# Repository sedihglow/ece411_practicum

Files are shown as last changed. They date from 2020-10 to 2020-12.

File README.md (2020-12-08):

# ece411_practicum
ece411 practicum project Team 16

# how to upload to ESP
1. Start upload from arduino IDE.
  - It will sit on connecting for this time.
2. Pull the reset pin low or unplug the device
3. Pull GPIO2 low with a button.
4. Let the reset pin go high or plug back in the device while gpio2 is low
  - The code should start uploading
5. let go of the GPIO2 button to ground.

# ESP setup program
1. Setup sensor pins
2. Setup I2C for moisture sensor
3. Try to connect to wifi using credentials in EEPROM
4. If credentials are bad, start a wifi hotspot on ESP
5. Connect to ESP using its wifi hotspot by connecting to the IP Address from a web browser
6. Once credentials are changed it reconnects using the new credentials.

# ESP main loop program flow
1. Check for user packet
2. if user sent a packet, handle the request for moisture threshold or pump time
3. read the moisture sensor
4. If the moisture sensor reads below threshold and water is in the tank, water plant
5. repeat 1-4

# user program
To compile use the makefile $make
To run you can use the makefile $make run
The user program will prompt the user with a menu
  - change moisture threshold
  - change pump time
  - exit program
  
The moisture threshold can be values of 1 to 1000

The pump time can be between 1 and 10 seconds

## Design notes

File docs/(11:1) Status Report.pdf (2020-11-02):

The Four COVIDeers
11/1/2020
Week 5 Status Report

Now that we are at the end of week five, our pace has started to pick up. Our main goals were to have all components in hand, test the components, and to have some prototypes by this time. We almost have all of the components, which are being tested, and have made some low-level prototypes.

We have completed a preliminary schematic and have begun working on our PCB design using Eagle CAD. Our team has also started to make a voltage regulator circuit for our esp8266 microcontroller. In the next two weeks, we plan on assembling our product and doing a large amount of coding. This would set aside the last few weeks for troubleshooting and making corrections.

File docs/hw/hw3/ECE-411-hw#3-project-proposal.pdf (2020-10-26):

# Project Design Specification

## The “Smart Irrigator”

Authors: Jakob White, Nathan Paul, Ahmad Alothaimin, James Ross

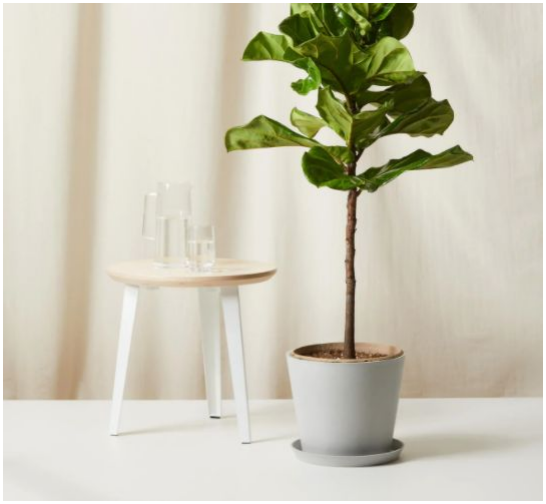
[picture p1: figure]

Date: Oct. 20, 2020
Version: 1.0

Concept of Operations

- Need Statement
Today, work occupies a majority of an individual’s time. Sometimes, a person might not be able to take care of their plants due to distractions. Being out of town for a period of time could also result in a house plant dying from lack of water. An irregular watering schedule for your plants could also lead to problems for the plants. Therefore, it is desirable to have an automated system to care for the plants.
- Objective Statement
What is our solution? The Smart Irrigator system can be a new addition to smart home devices in a society where home automation is taking off. It is an auto-irrigation system intended for small-scale indoor plants that automatically hydrates the soil depending on the current moisture level in the soil. Therefore, rather than worrying about whether or not you watered your plants, the Smart Irrigator will automatically do it for you.
- Who Uses It? Why?
This watering system can be used by horticulturalists, hobbyists, or anyone who owns a small-scale indoor plant. To use this system, the user will first set up their chosen plant with the Smart Irrigator (including a water reservoir of their choice). They will then use our app on their laptop to customize their plant-watering preferences, which will include options for either a timer-based watering schedule or fully-automated, sensor-based watering.

Market Analysis

This product is intended for anyone with an interest in growing small-scale indoor plants, but does not want to spend too much time tending to them. This device will particularly be directed towards people in the age range of 20-35 years old who own house plants. As for competition, there are a few products that are similar to ours. One competitor is the MAYiT Garden Automatic Drip watering system, which uses a timer to water the plants. Many other competitors also have timers, and some must even be plugged into an outlet. Our product will be different because it will use a moisture sensor that will detect when the plant needs to be watered, which will then activate a pump. Our device will be powered by batteries and will also notify the user when more water needs to be added to the reservoir. Given the materials we expect to use, the unique features of our product, and the widespread interest in having indoor plants among various demographics (coupled with a disinterest in maintaining them), we expect to sell our product at around $50.

Requirements

- Functionality
- The product must sense moisture level in the soil of small-scale potted plants.
- The product must receive user input to establish a watering schedule.
- The product must sense the water level in the water reservoir.
- The product must process input from the moisture sensor to determine whether the plant needs to be watered.

- The product must process input from the water-level sensor to determine whether or not the water reservoir is empty.
- When the plant needs water, the product must actuate a water pump to water the plant.
- When the reservoir is empty, the product must not actuate the water pump.
- The product should notify the user if the water reservoir is empty.
- The product may notify the user if batteries are low.
- The product may monitor the plant’s exposure to natural sunlight to provide artificial sunlight if the plant is not properly exposed.
- The product must employ Wi-Fi to enable the user to change his watering preferences.
- The product should operate using an Arduino program.
- Energy
- The product should be battery operated.
- The product should have a battery life of at least one month.
- The product may be solar powered.
- Operational
- The product should be adaptable to any small-scale potted plant.
- Maintainability
- The product should notify the user when an error occurs in the system.

System Architecture

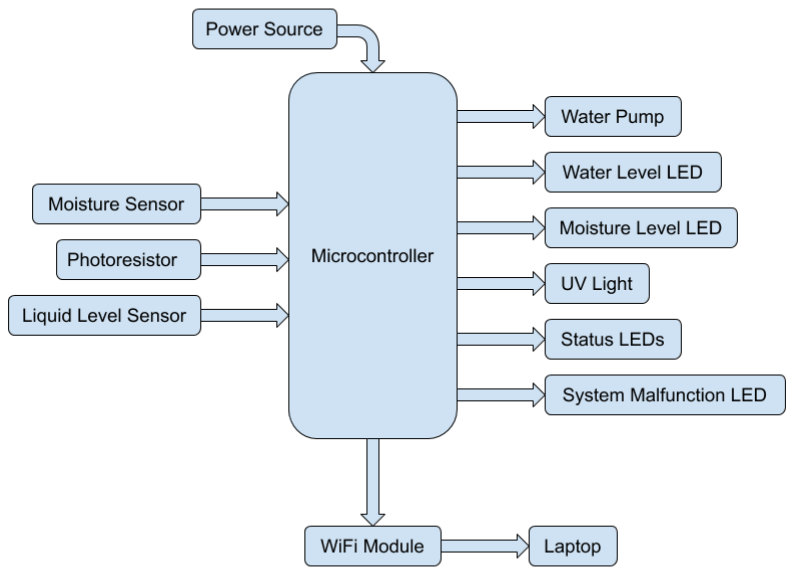
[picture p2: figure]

Figure I: Level I diagram of the Smart Irrigator

Design Specification

- Sensors
- Non-contact Digital Water/Liquid Level Sensor
- Analog Capacitive Soil Moisture Sensor
- Processor
- Esp8266 nodemcu
- Actuator
- Water Pump
- Multicolor LEDs
- Power
- 3.3V voltage regulator
- 3.7V lithium ion polymer battery
- Development Environment
- Arduino IDE

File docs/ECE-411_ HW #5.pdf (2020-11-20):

Names: Jakob White, Nathan Paul, Ahmad Alothaimin, James Ross Date: Nov. 19, 2020

# Detailed Design

Level-0 Design

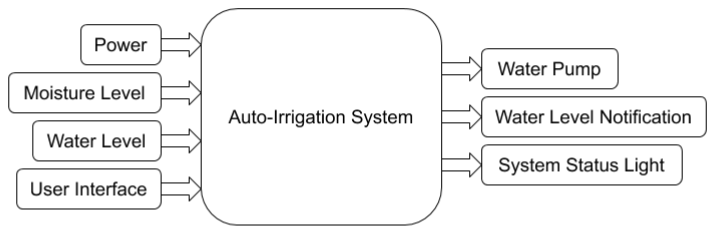
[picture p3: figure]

Module | Auto-Irrigation System
Inputs | Power: 3.6V Moisture Level: Variable Water Level: Variable User Interface: Variable (Watering Schedule Control)
Outputs | Water Pump: Water to Plant Water Level Notification: WiFi Notification to Refill Reservoir System Status Light: Light Indicating System Status
Functionality | This system automatically waters indoor plants. If the moisture level is below a certain level and the water reservoir is not empty, the plant is watered. Else, the plant is not watered. The user should be notified when the water reservoir is empty.

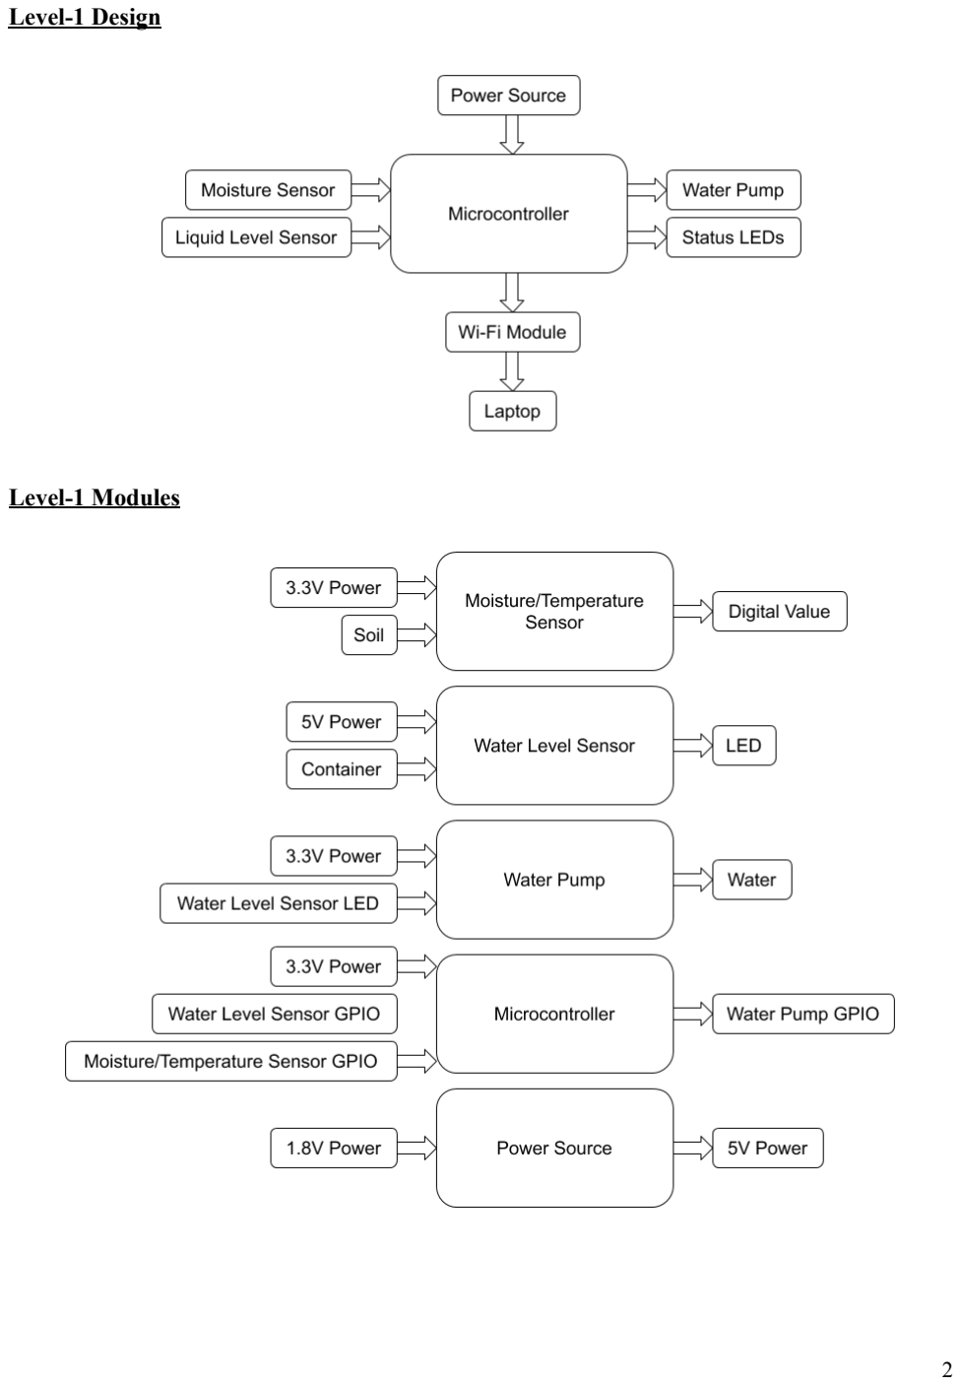
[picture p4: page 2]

Level-1 Design

Level-1 Modules

Module | Moisture/Temperature Sensor
Inputs | Power: 3.3V Soil: Moist or dry
Outputs | Digital values: Capacitive for soil moisture, temperature in celsius
Functionality | This gives a capacitance reading ranging from about 200 (very dry) to 2000 (very wet). The component also gives a temperature from the internal temperature sensor on the microcontroller. However, the margin of error is + or - 2 degrees celsius.
Module | Water Level Sensor
Inputs | Power: 5V Container: with or without water
Outputs | LED: Indicates whether the water is below a certain level.
Functionality | This component is able to detect the water level from contacting the container alone. The presence of water or absence thereof results in the LED being on or off. There are no special requirements for the liquid or container to be used.
Module | Power Source
Inputs | Charge
Outputs | Voltage and Current
Functionality | The power source provides voltage (3.7V) and current (2200 mA).
Module | Water Pump
Inputs | Actuation Signal from Microprocessor
Outputs | Water to the Soil.
Functionality | The purpose of the water pump is to water the plant whenever the soil is below a certain threshold of moisture.
Module | Wifi Module
Inputs | Water Reservoir Data from Microprocessor
Outputs | Wifi Notification to User’s Device

Functionality | The purpose of this module is to send data to the user’s chosen device to notify when the water reservoir is empty.
Module | Status LED
Inputs | Actuation Signal from Microprocessor
Outputs | Light from LED
Functionality | The purpose of this LED is to notify the user that the system is ON and functioning.

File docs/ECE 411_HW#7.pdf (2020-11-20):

Names: Jakob White, Nathan Paul Ahmad Alothaimin, James Ross Date: Nov. 19, 2020

## Peer Design Review

On Nov. 17, 2020, our team exchanged schematics with Team #14 and exchanged feedback on our designs.

Project: Automatic Bird Feeder
Description: An automatic bird food dispenser that detects bird motion to dispense food.
Review of our schematic:
- Schematic needs to flow from left to right.
- Rename serial port. Describe the serial port function.
- Label inputs and outputs (data flow).
- Use boxes for circuit blocks.

On Nov. 17, 2020, our team met with Team #17 to discuss our designs.

Project: Manual Hole Disc Player.
Description: Device reads disc based on flaps, 4 bits per time, plays music. Review of our schematic:
- Through holes will need to be done ourselves.
- Buy headers for through holes.
- Place the vias on the corners of the board? Use vias wherever you want a through-hole component.
- Type of resistors: shouldn’t matter too much. Look at data sheets for dimensions.
- Jameco.com to buy components.
- Use a larger power transistor: T0220, TIP31.
- Diodes for voltage kickback. Place it for the water pump.
- Add capacitors to the power pins on the IC.

On Nov. 18, 2020, our team met with Andrew Greenberg to discuss our schematic and PCB design.

Review of our schematic:
- Where is the power in the schematic? The lithium ion battery will power the ESP through a 3.3V voltage regulator.
- Copy the ground symbol multiple times rather than using wires in the schematic.
- Put a power boost block into the schematic as well.
- I2C requires 4.7k pull-up resistors. SDA and SCL. Label these as well.
- Change the 10k resistors to 4.7k resistors.
- Use headers.
- Through holes are acceptable, although he would push toward using a surface mount.
- Label everything and put notes.
Review of our PCB:
- Mark everything. Make the power lines thick.

- Put a ground plane on the bottom as well.
- Put vias every ½-1 inch.

On Nov. 18, 2020, our team met with Team #8 to discuss our designs after finalizing our schematic and PCB layout.

Project: Facial Recognition Smart Door Lock.
Description: Raspberry Pi camera scans face to verify correct identity to unlock a door.
Review of our schematic:
- Think about how long the battery will last, since our device needs to be functional for a long time.
- Label functionality of button for reset.

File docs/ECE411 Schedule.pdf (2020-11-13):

1 | Hardware | 75 days | 11/12/20 5:00 PM | 12/7/20 5:00 PM
2 | Finish breadboard design | 3 days | 11/12/20 5:00 PM | 11/13/20 5:00 PM
3 | Encase PCB and sensors | 0 days | 12/5/20 9:05 AM | 12/7/20 5:00 PM | 12
4 | Software | 64 days | 11/13/20 9:00 AM | 12/4/20 5:00 PM
5 | Code hardware tests | 1 day | 11/13/20 9:00 AM | 11/13/20 5:00 PM
6 | Code processor | 5.875 days | 11/18/20 9:00 AM | 11/25/20 5:00 PM
7 | Test and debug code | 24 days | 11/26/20 5:00 PM | 12/4/20 5:00 PM | 6
8 | Integration | 26.625 day... | 11/18/20 12:00 PM | 11/27/20 9:00 AM
9 | Assemble breadboard | 0.625 days? | 11/18/20 12:00 PM | 11/18/20 5:00 PM | 16
10 | Print PCB | 2 days? | 11/18/20 5:00 PM | 11/20/20 5:00 PM | 20
11 | Assemble PCB | 4.125 days? | 11/23/20 8:00 AM | 11/27/20 9:00 AM | 10
12 | Testing | 54 days? | 11/16/20 5:00 PM | 12/4/20 5:00 PM
13 | Test processor | 1 day | 11/16/20 5:00 PM | 11/17/20 5:00 PM | 5
14 | Test voltage regulator | 1 day | 11/16/20 5:00 PM | 11/17/20 5:00 PM | 5
15 | Test moisture sensor | 1 day | 11/16/20 5:00 PM | 11/17/20 5:00 PM | 5
16 | Test pump driver | 1 day | 11/16/20 5:00 PM | 11/17/20 5:00 PM | 5
17 | Test full breadboard circuit | 3 days? | 11/18/20 5:00 PM | 11/19/20 5:00 PM | 9
18 | Test PCB and sensors | 22 days? | 11/27/20 9:00 AM | 12/4/20 5:00 PM | 11
19 | Documentation | 81.375 day... | 11/12/20 2:00 PM | 12/9/20 5:00 PM
20 | Refurbish schematic and layout | 3.375 days? | 11/12/20 2:00 PM | 11/17/20 5:00 PM
21 | Compile Bill of Materials | 0.375 days? | 11/12/20 2:00 PM | 11/12/20 5:00 PM
22 | Develop testing plan | 15.375 days? | 11/12/20 2:00 PM | 11/17/20 5:00 PM
23 | Sign up for demo | 4 days? | 11/29/20 9:00 AM | 11/30/20 5:00 PM
24 | Demo practicum project | 1 day? | 12/9/20 9:00 AM | 12/9/20 5:00 PM
Name | Duration | Start | Finish | Predecessors

ECE411 Schedule - page1

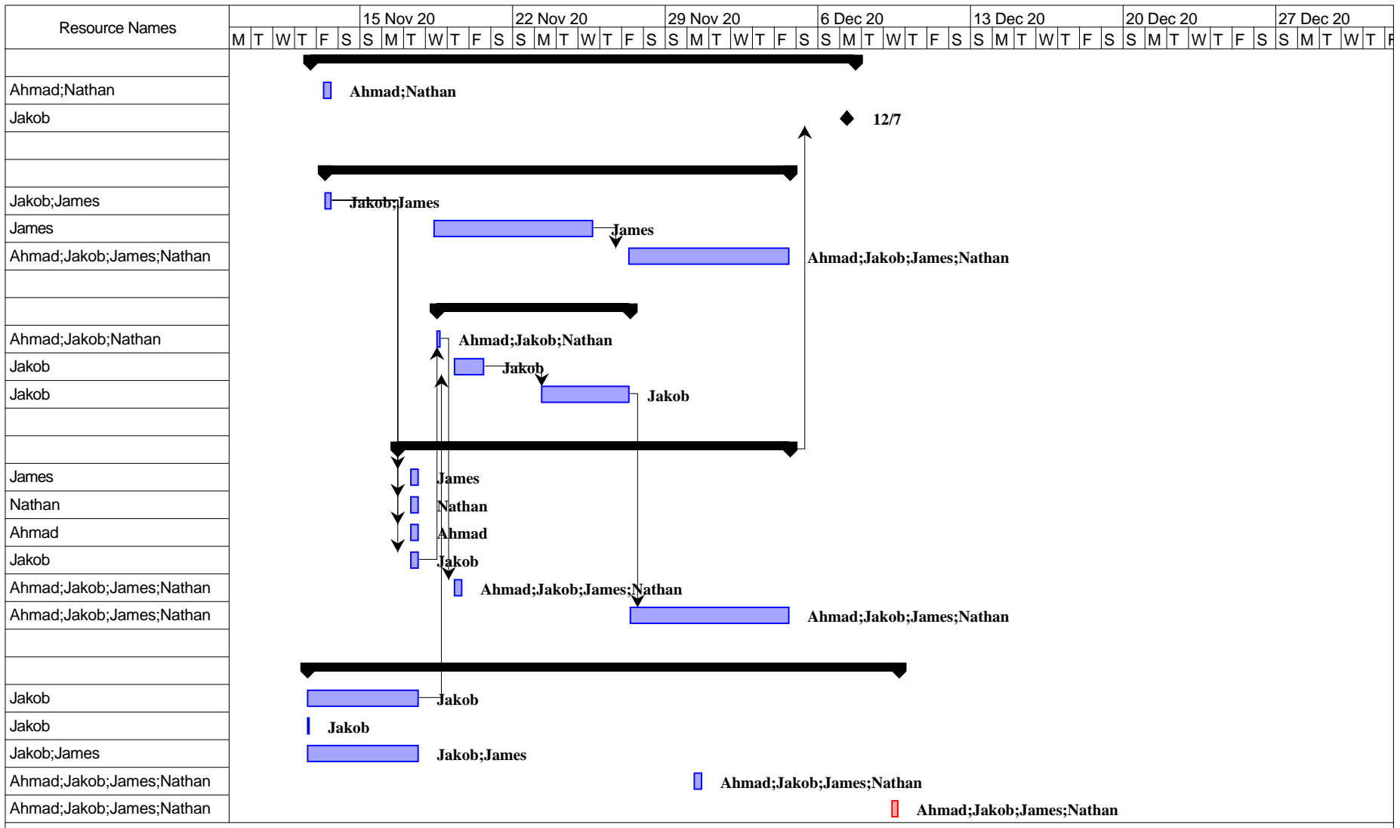
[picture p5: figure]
15 Nov 20; 22 Nov 20; 29 Nov 20; 6 Dec 20; 13 Dec 20; 20 Dec 20; 27 Dec 20; Ahmad;Nathan Jakob; Jakob;James James Ahmad;Jakob;James;Nathan; Ahmad;Jakob;Nathan Jakob Jakob; James Nathan Ahmad Jakob Ahmad;Jakob;James;Nathan Ahmad;Jakob;James;Nathan; Jakob Jakob Jakob;James Ahmad;Jakob;James;Nathan Ahmad;Jakob;James;Nathan; Resource Names; Ahmad;Nathan; Jakob;James; James; Ahmad;Jakob;James;Nathan; Ahmad;Jakob;Nathan; Jakob; Nathan; Ahmad

ECE411 Schedule - page2

T | W | T | F | S | S 3 Jan 21
M | T | W | T | F

ECE411 Schedule - ...

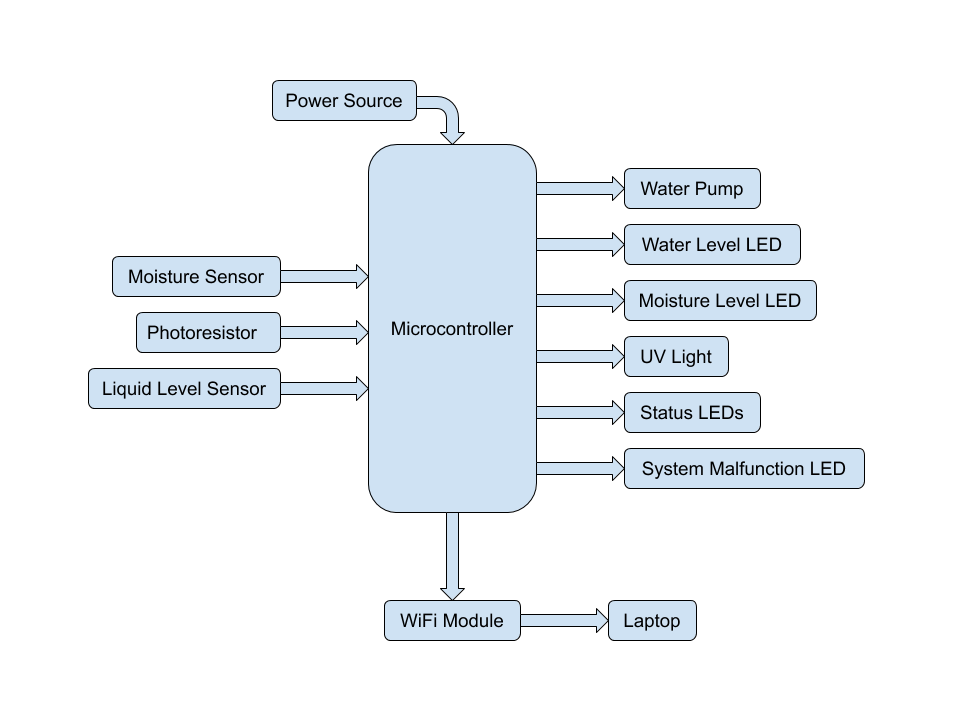
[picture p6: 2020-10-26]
docs/block_diagrams/block_diagram_lvl1.png

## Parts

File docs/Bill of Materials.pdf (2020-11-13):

# Bill of Materials

Team #16: Les Quatre COVIDeers

Quantity | Reference
Designator

Manufacturer Manufacturer
Part No.

Description

1 | IC1 | AI Thinker | ESP-12F (ESP8266MOD) | ESP-12E/F Integrated Chip
2 | VCC | Samsung | 18650 | 3.7V Rechargeable Battery
1 | Moisture Level Sensor | Adafruit | 4026 | Soil Moisture Sensor
1 | Water Level Sensor | DFRobot | XKC-Y25-T12V SKU SEN0204 | Water Level Sensor
1 | Water Pump | GikFun | EK1893 | Water Pump
1 | R1 | Jameco Valuepro | CF1/4W102JRC | 1k Resistor
5 | R2, R3, R4, R5, R6 | Jameco Valuepro | CF1/4W103JRC | 10k Resistor
1 | S1 | TE Connectivity | 1825967-2 | Switch
1 | Voltage Regulator | STMicroelectronics | LD1117V33 | Voltage Regulator

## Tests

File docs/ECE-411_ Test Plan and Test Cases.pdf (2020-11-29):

# Test Plan for the Auto-Irrigator

### Authors: Jakob White, Nathan Paul, James Ross, Ahmad Alothaimin

### Date: Nov. 27, 2020 Revision: 1.0

### System Under Test

The subject of this test plan is the Auto-Irrigator V. 1.2, which is essentially the same as the original version with the subtraction of a few excess features such as LED illumination of the plant.

### Objectives

The overall purpose of this test plan is to confirm our breadboard design of the Auto-Irrigator and validate the construction of a final PCB circuit. Specifically, the first goal of this test plan is to perform unit tests on each module. The second goal is to perform iterative integration testing in which one module is added at a time to the processor and the system is tested. Once the system has been entirely assembled, we shall perform functional testing. Parametric testing will also be performed to determine the battery life.

### Resources

- Hardware
- One Auto-Irrigator V. 2.0
- One potted plant
- One vase filled with water
- Tubing for water pump
- Windows 10 PC
- Multimeter
- Software
- Test script for each module V. 1.0
- Test script for full system V. 1.0
- Personnel
- One person with basic knowledge of coding, electronic hardware, and microcontrollers ■ Basic system training/study required

1

### Outline

### 1. Unit Testing 1.1. Power Supply Test Case: Testing to confirm 5V and 3.3V VCC

1.2. Processor Test Case: Testing to confirm that the processor receives code.
1.3. WiFi Test Case: Testing to confirm that the processor transmits data over WiFi.
1.4. Water Level Sensor Test Case: Testing to confirm that the processor detects input from the water level sensor.
1.5. Moisture Sensor Test Case: Testing to confirm that the processor detects input from the moisture sensor.

### 1.6. Water Pump Test Case: Testing to confirm that the water pump and its associated

transistor switch can be actuated by the processor and powered by the power supply.

### 2. Integration Testing

2.1. Moisture Detection Test Case: A half-system test to confirm that the processor actuates the water pump when moisture is not detected in the soil.
2.2. Empty Reservoir Detection Test Case: A half-system test to confirm that the processor does not actuate the water pump when the water reservoir is empty.

### 3. Functional Testing 3.1. Short-Term Operation Test Case: A full-system test to confirm successful short-term

operation.

### 4. Parametric Testing

4.1. Battery Life Test Case: A full-system test to confirm long-term battery life.

2

### Test Case #1

3

Test Author: Jakob White

Test Case Name: | Power Supply Test Case | Test ID#: | 1.1
Description: | This test confirms the rated output voltage of the voltage regulator and the Power Boost. The power source is not loaded during the test. | Type: | Unit Test

Tester Information

Name of Tester: | | Date:
Hardware Version: | Power Supply of Auto-Irrigator V. 1.2 | Time:
Setup: | Before testing, the power supply module should be disconnected from the system and the battery should be fully charged. Once fully charged, battery power should be applied to the input of the power boost. With the multimeter, the output voltage at the ‘5V’ terminal of the power boost and the ‘3.3V’ output of the voltage regulator should be measured.
Step: | Action: | Expected Result: | P/NP: | Comments:
1 Disconnect Power | Supply from System | The power supply should be isolated
2 | Charge Battery | The battery should be fully charged
3 Connect Battery to | ‘BAT’ and ‘GND’ of Power Boost | The battery should power the power supply
4 Measure Voltage | between ‘5V’ and ‘GND’ of Power Boost | The multimeter should indicate 5V
5 Measure Voltage | between ‘3.3V’ and ‘GND’ of voltage regulator | The multimeter should indicate 3.3V

Overall Test Results:

### Test Case #2

4

Test Author: Jakob White

Test Case Name: | Water Pump Test Case | Test ID#: | 1.6
Description: | This test confirms that the output from GPIO#5 of the processor can switch on the water pump using a transistor, and that the power supply to the water pump is enough for this application. | Type: | Unit Test

Tester Information

Name of Tester: | | Date:
Hardware Version: | Water Pump of Auto-Irrigator V. 1.2 | Time:
Setup: | Before testing, make sure that the only modules connected are the power supply, the processor, the water pump, and the switch transistor. The base of the transistor should be connected to GPIO#5, and the water pump should be between the 3.3V power supply and the collector. A water pump test script should be prepared to simply turn GPIO#5 to HIGH output.
Step: | Action: | Expected Result: | P/NP: | Comments:
1 Download the test | code for the water pump on to the processor | The code should be successfully downloaded
2 | Execute the script | The motor should be turned on and stay on.

Overall Test Results:

### References

Faust, Mark. “Homework #7: Test Plan.” Portland State University, 2020, d2l.pdx.edu/d2l/le/content/823599/viewContent/5068014/View.

Faust, Mark. “Test Plan Rubric.” Capstone Website, 2020, web.cecs.pdx.edu/~faustm/capstone/forms/TestPlanRubric.pdf.

Faust, Mark. “Lecture #8: Testing and Documentation.” Portland State University, 2020, https://d2l.pdx.edu/d2l/le/content/823599/viewContent/5068012/View.

5

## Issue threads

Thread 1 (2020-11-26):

Water pump power

sedihglow, 2020-11-26:
Not getting enough current through the transistor to drive the pump

sedihglow, 2020-12-03:
Solved current through the resistor to drive the pump but now getting wdt resets upon operation.

Closed 2020-12-03.

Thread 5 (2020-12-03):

wdt resets from water pump

sedihglow, 2020-12-03:
pump but now getting wdt resets upon operation.

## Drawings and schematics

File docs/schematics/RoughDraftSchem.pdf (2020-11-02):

# ESP-12E/F ⁵V

A

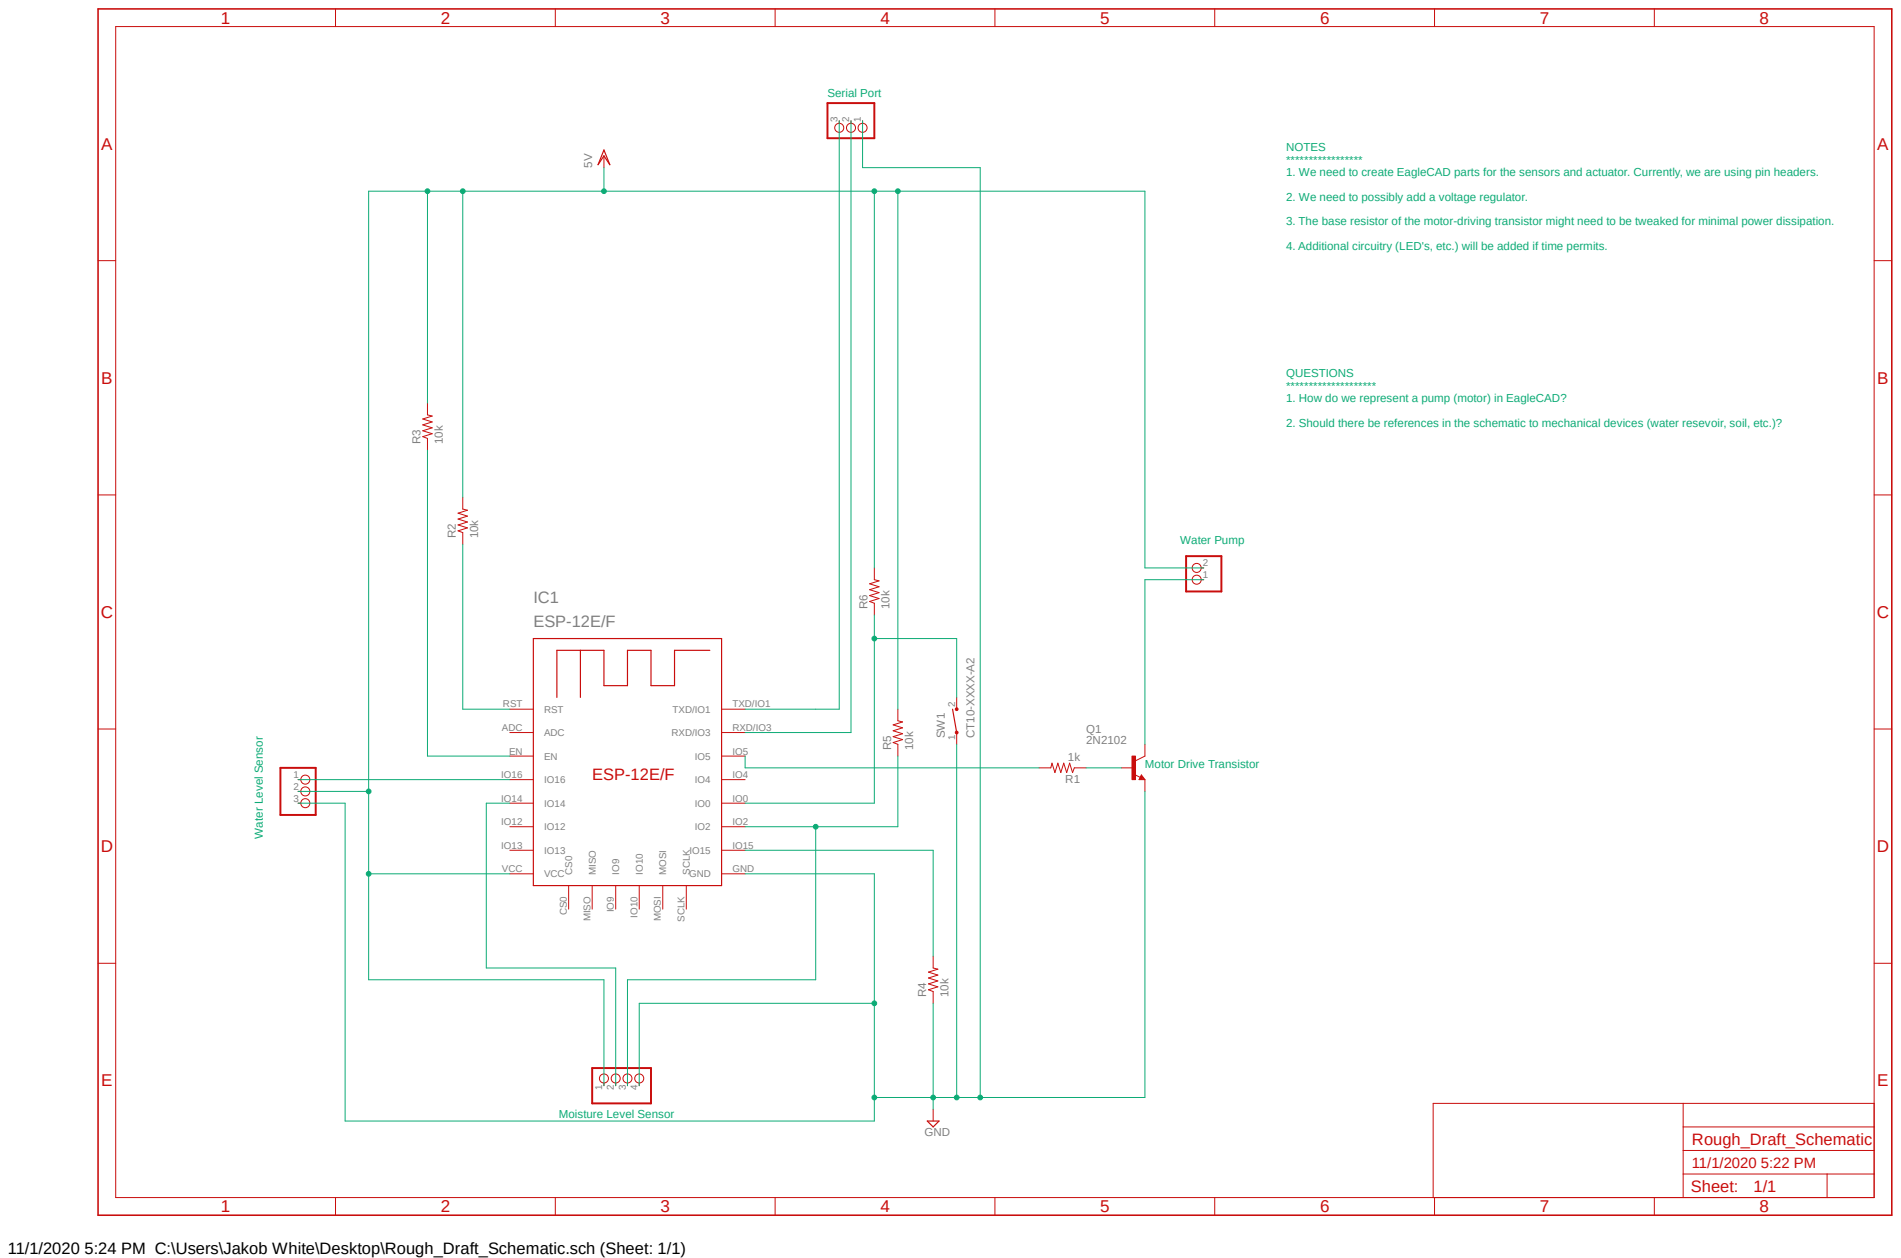
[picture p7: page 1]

NOTES
***************** 1. We need to create EagleCAD parts for the sensors and actuator. Currently, we are using pin headers.

2. We need to possibly add a voltage regulator.
3. The base resistor of the motor-driving transistor might need to be tweaked for minimal power dissipation.
4. Additional circuitry (LED's, etc.) will be added if time permits.

QUESTIONS
******************** 1. How do we represent a pump (motor) in EagleCAD?

2. Should there be references in the schematic to mechanical devices (water resevoir, soil, etc.)?

11/1/2020 5:24 PM C:\Users\Jakob White\Desktop\Rough_Draft_Schematic.sch (Sheet: 1/1)

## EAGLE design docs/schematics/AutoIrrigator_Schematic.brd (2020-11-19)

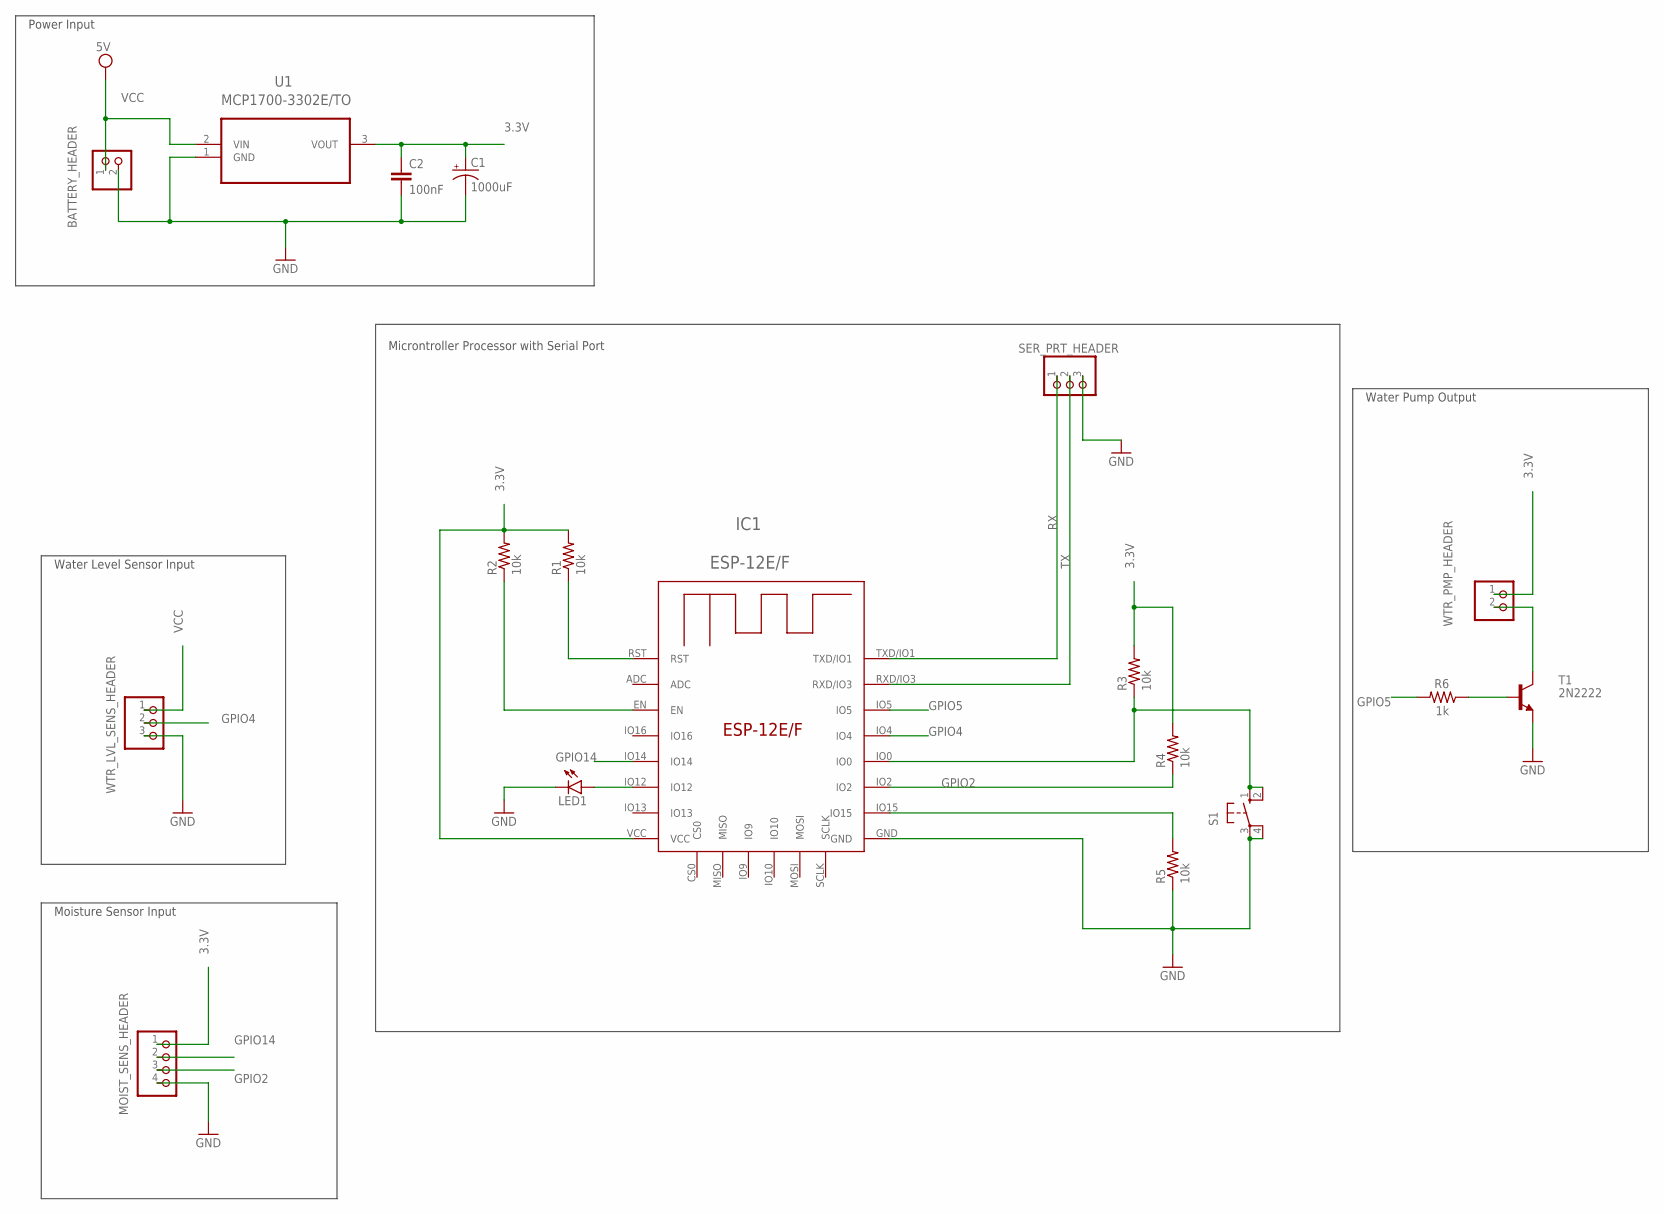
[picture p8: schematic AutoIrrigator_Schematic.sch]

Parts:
BATTERY_HEADER: PINHD-1X2; 1X02
C1: 1000uF; E2,5-6
C2: 100nF; C025-025X050
IC1: ESP-12E/F; ESP-12E
LED1: LED5MM
MOIST_SENS_HEADER: PINHD-1X4; 1X04
R1, R2, R3, R4, R5: 10k; 0204/7
R6: 1k; 0204/7
S1: 10-XX; B3F-10XX
SER_PRT_HEADER: SER_PRT_HEADER; 1X03
T1: 2N2222; TO18
U1: MCP1700-3302E/TO; TO127P254X495-3
WTR_LVL_SENS_HEADER: PINHD-1X3; 1X03
WTR_PMP_HEADER: PINHD-1X2; 1X02

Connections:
3.3V: C1.+, C2.1, IC1.VCC, MOIST_SENS_HEADER.1, R1.2, R2.2, R3.2, R4.2, U1.3 (VOUT), WTR_PMP_HEADER.1
COLLECTOR: T1.3 (C), WTR_PMP_HEADER.2
EMITTER: R6.1, T1.2 (B)
EN: IC1.EN, R2.1
GND: BATTERY_HEADER.2, C1.-, C2.2, IC1.GND, LED1.K (C), MOIST_SENS_HEADER.4, R5.1, S1.3, S1.4 (P1), SER_PRT_HEADER.3, T1.1 (E), U1.1 (GND), WTR_LVL_SENS_HEADER.3
GPIO0: IC1.IO0, R3.1, S1.1 (S), S1.2 (S1)
GPIO2: IC1.IO2, MOIST_SENS_HEADER.3, R4.1
GPIO4: IC1.IO4, WTR_LVL_SENS_HEADER.2
GPIO5: IC1.IO5, R6.2
GPIO12: IC1.IO12, LED1.A
GPIO14: IC1.IO14, MOIST_SENS_HEADER.2
GPIO15: IC1.IO15, R5.2
RST: IC1.RST, R1.1
RX: IC1.TXD/IO1, SER_PRT_HEADER.1
TX: IC1.RXD/IO3, SER_PRT_HEADER.2
VCC: BATTERY_HEADER.1, U1.2 (VIN), WTR_LVL_SENS_HEADER.1

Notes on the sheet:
Water Level Sensor Input
Power Input
Moisture Sensor Input
Microntroller Processor with Serial Port
Water Pump Output

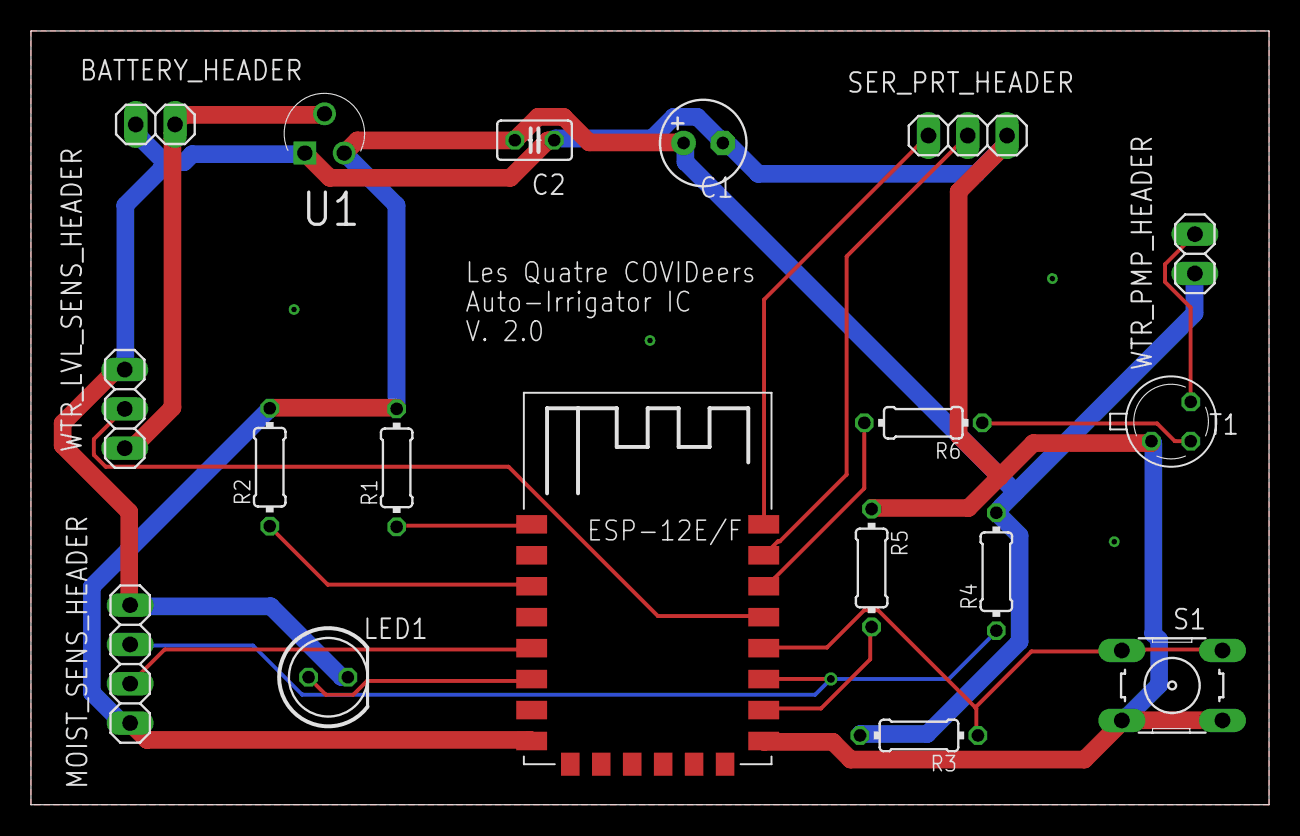
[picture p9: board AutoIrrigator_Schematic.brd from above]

Board: 2 copper layers, 80.0 x 50.0 mm, 18 parts (0 on the bottom side), 16 nets.

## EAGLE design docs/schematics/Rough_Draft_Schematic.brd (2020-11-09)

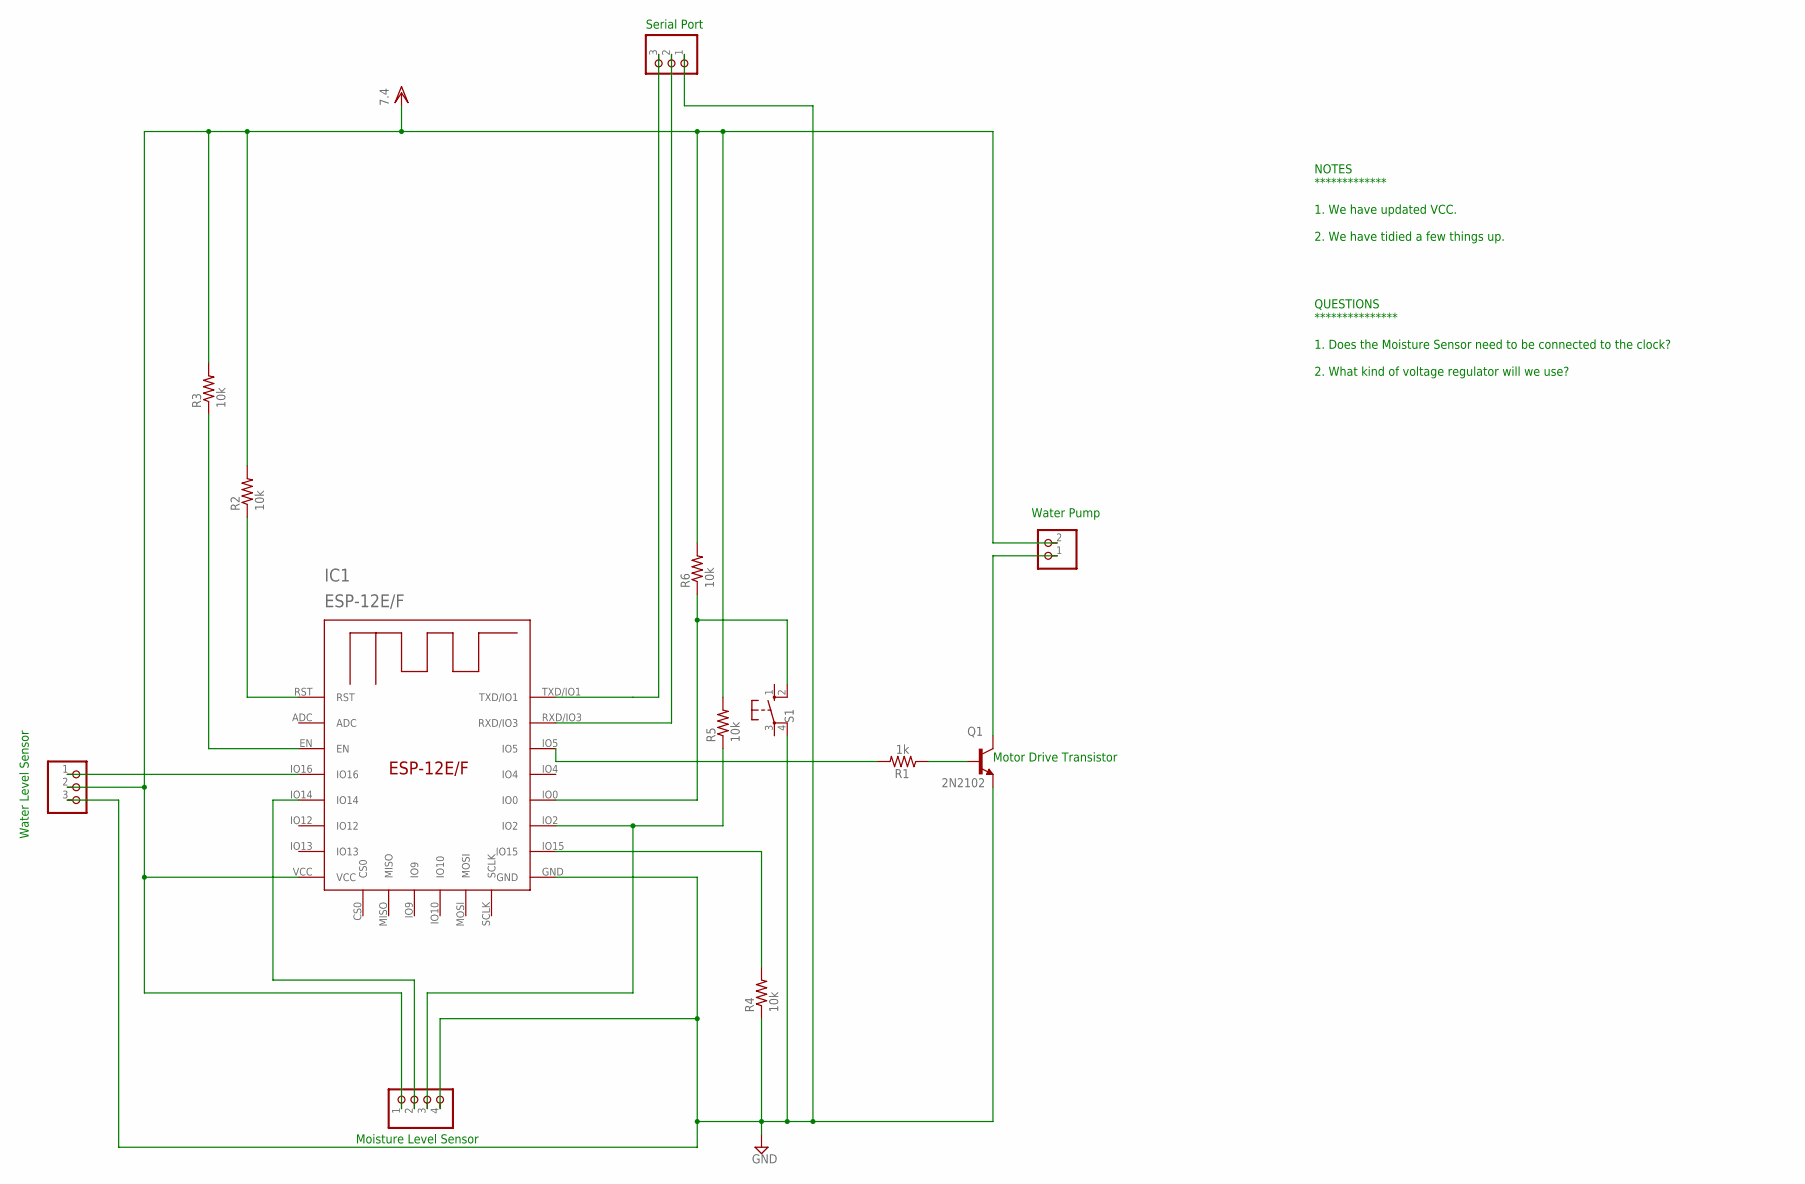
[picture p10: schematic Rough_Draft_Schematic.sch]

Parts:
IC1: ESP-12E/F; ESP-12E
JP1: PINHD-1X2; 1X02
JP3, JP4: PINHD-1X3; 1X03
JP5: PINHD-1X4; 1X04
Q1: 2N2102; TO5
R1: 1k; 0204V
R2, R3, R4, R5, R6: 10k; 0204V
S1: 10-XX; B3F-10XX

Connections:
GND: IC1.GND, JP3.3, JP4.1, JP5.4, Q1.1 (E), R4.1, S1.4 (P1)
MOISTURE_SENSOR: IC1.IO2, JP5.3, R5.1
unnamed: IC1.IO15, R4.2
unnamed: IC1.RXD/IO3, JP4.2
unnamed: IC1.EN, R3.1
unnamed: IC1.RST, R2.1
unnamed: IC1.IO0, R6.1, S1.2 (S1)
unnamed: IC1.IO14, JP5.2
unnamed: IC1.IO5, R1.2
unnamed: Q1.2 (B), R1.1
unnamed: JP1.1, Q1.3 (C)
VDD: IC1.VCC, JP1.2, JP3.2, JP5.1, R2.2, R3.2, R5.2, R6.2
WATER_LEVEL_SENSOR: IC1.IO16, JP3.1

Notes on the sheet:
Water Level Sensor
Moisture Level Sensor
Serial Port
Water Pump
Motor Drive Transistor
NOTES ************* 1. We have updated VCC. 2. We have tidied a few things up. QUESTIONS *************** 1. Does the Moisture Sensor need to be connected to the clock? 2. What kind of voltage regulator will we use?

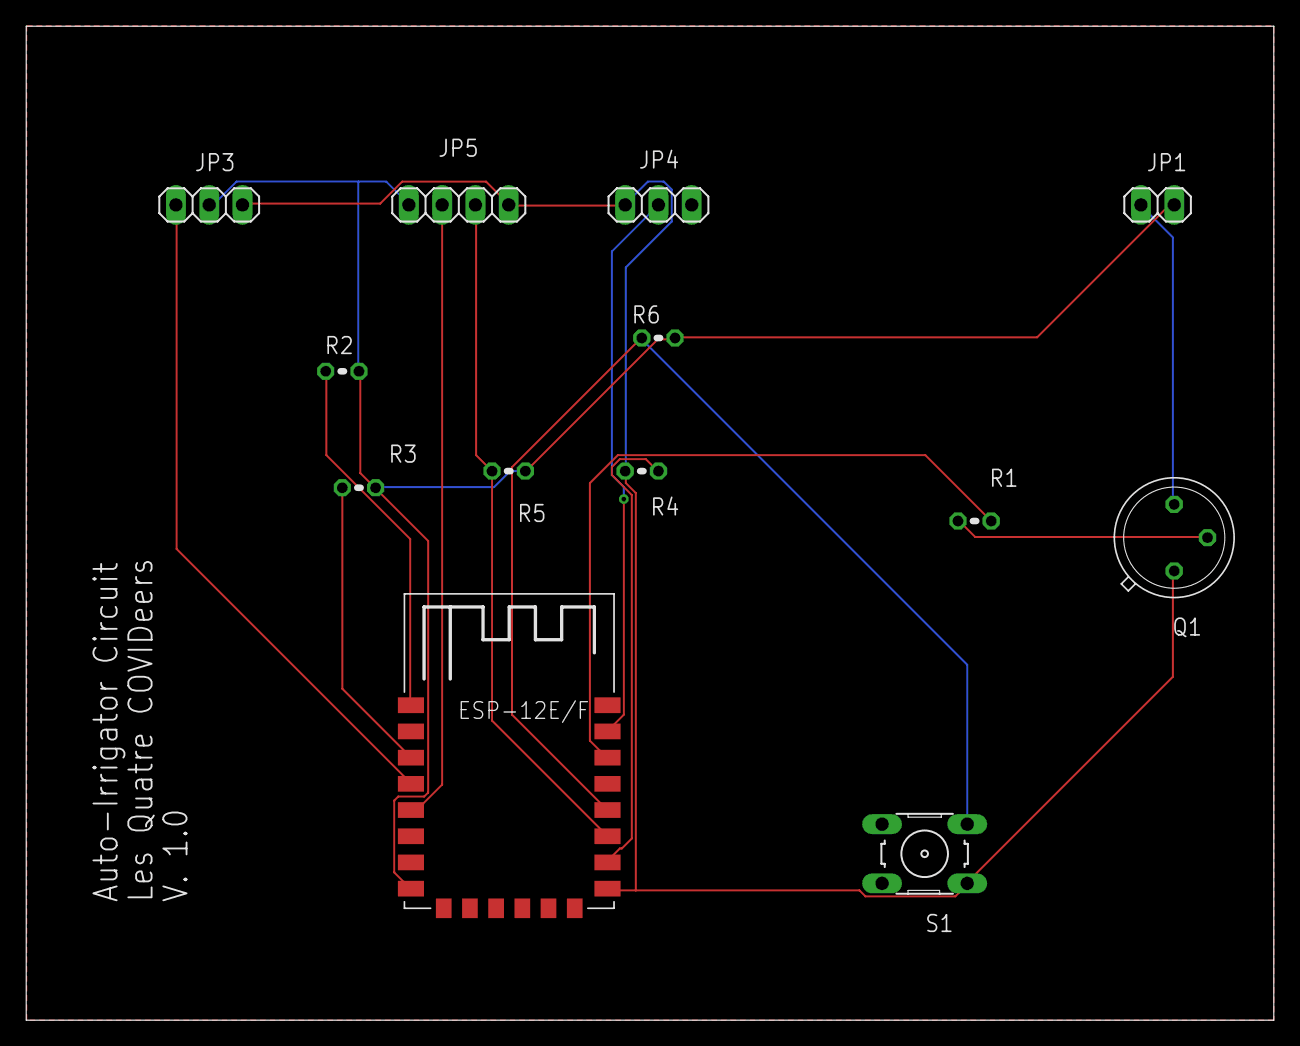
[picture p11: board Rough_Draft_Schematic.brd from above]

Board: 2 copper layers, 95.2 x 75.9 mm, 13 parts (0 on the bottom side), 13 nets.

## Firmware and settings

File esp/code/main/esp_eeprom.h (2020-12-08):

#ifndef ESP_EEPROM_H
#define ESP_EEPROM_H

#include <EEPROM.h>
#include "moisture.h" // for default values
#include "pump.h" // for default values

#define EEPROM_SIZE 512
#define UNINIT_PUMP_VALUE_THRESH 51
#define SSID_SIZE 32
#define PASS_SIZE 31
#define DEFAULT_SSID "DEFAULT_SSID" //"ASUS_88_2G" "DEFAULT_SSID"
#define DEFAULT_PASS "DEFAULT_PASS" //"goodness"

typedef struct eeprom_data {
    char ssid[SSID_SIZE];
    char pass[PASS_SIZE];
    uint16_t moisture_thresh;
    int pump_time; // in seconds, cannot be over UNINIT_PUMP_VALUE_THRESH
} data_s;

void init_eeprom_data(data_s *init_data);

void change_mthresh(data_s *data, int num);
void change_pump_time(data_s *data, int num);

void test_get_eeprom_data(data_s *data);
#endif

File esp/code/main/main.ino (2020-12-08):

#include "hw.h"
#include "moisture.h"
#include "external_led.h"
#include "water_sensor.h"
#include "pump.h"
#include "esp_eeprom.h"
#include "irrigator_wifi.h"

Adafruit_seesaw moisture_sensor; // moisture sensor class
data_s edata; // eeprom data for operation

uint16_t moisture_read = 0;
int water_read = 0;
int led_blink = HIGH;

WiFiUDP udp;
unsigned int local_udp_port = UDP_PORT; // listens on this port
char incoming_packet[PACKET_BUFF_SIZE] = {'\0'}; // buffer for incoming packets
int packet_size = 0;
int len = 0;

void setup()
{
    int ret = SUCCESS;
    int start_addr = 0;
    data_s init_test_data; // used to test if eeprom is initialized

    Serial.begin(BAUD_RATE);
    Serial.print('\n'); // newline for garbage terminal produces on boot
    
    // initialize data with default values
    init_eeprom_data(&edata);

    // if eeprom is uninitialized, initialize it.
    EEPROM.begin(EEPROM_SIZE);
    EEPROM.get(start_addr, init_test_data);
    if (init_test_data.pump_time > UNINIT_PUMP_VALUE_THRESH ||
        init_test_data.pump_time < 1) {
        Serial.println("storing init edata to eeprom");
        EEPROM.put(start_addr, edata);
        EEPROM.commit();
    }

    // setup external led pin to output
    setup_led_out();

    // setup i2c moisture sensor
    ret = setup_moisture_sensor(&moisture_sensor);
    if (ret) {
        Serial.println("ERROR  moisture sensor not found");
        while(true); // if no moisture sensor do nothing
    } else {
        Serial.println("Success, moisture sensor found");
    }

    // setup water sensor as input
    setup_water_sensor();
    Serial.println("water sensor pin setup");

    // setup pump pin as output
    setup_pump_pin();
    Serial.println("pump pin setup");

    // setup wifi, if wifi not connected creates hotspot which can change
    // ssid and password, saves new credentials to eeprom.
    setup_wifi();

    // print local ip address of ESP
    Serial.print("IP address: ");
    Serial.println(WiFi.localIP());

    udp.begin(local_udp_port);
    Serial.printf("Now listening at IP %s, UDP port %d\n", 
                  WiFi.localIP().toString().c_str(), local_udp_port);
}

void loop()
{
    set_led(&led_blink);

    // check if we have any messages from user
    packet_size = udp.parsePacket();
    if (packet_size) {
        Serial.printf("Received %d bytes from %s, port %d\n",
                      packet_size, udp.remoteIP().toString().c_str(), 
                      udp.remotePort());
        len = udp.read(incoming_packet, PACKET_BUFF_SIZE);
        if (len > 0)
            incoming_packet[len] = '\0';
        
        handle_user_request(incoming_packet);
    }


    moisture_read = read_moisture(&moisture_sensor); 
    Serial.println("moisture reading: " +String(moisture_read));

    water_read = read_water_sensor();
    if (!water_read)
        Serial.println("water level low");
    
    // if there is still water in the tank and moisture is low
    if (water_read && moisture_read < edata.moisture_thresh) {
        Serial.println("water being pumped for " +String(edata.pump_time)
                     +" seconds");

        // start water pump for x seconds
        pump_water(edata.pump_time);
        delay(5000); // wait for soil to absorb water
    }

    delay(1000);
}

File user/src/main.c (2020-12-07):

#include "comm.h"
#include "user.h"

int main(void)
{
    serv_info_s *serv_info = NULL;
    char *user_input = NULL;

    serv_info = com_init_serv_info();
    if (!serv_info)
        errExit("main: failed to init serv_info");

    /* fill serv_info struct and initialize connection to server */
    init_client_comm(serv_info);

    
    for ( ;; ) {
        display_clear();
        display_welcome();
        display_menu();
        display_prompt();

        /* get user input */
        user_input = get_user_input();
        user_input[MENU_IN_LEN] = '\0';
        if (strcmp(user_input, STR_EXIT) == 0)
            break;

        exec_user_input(serv_info, user_input);
        free(user_input);
    }
    
    free(user_input);
    com_free_serv_info(serv_info);

}

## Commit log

2020-11-26 put appropriate files in docs, wrote inital tests for leds, water pump, water level sensor.
    [AutoIrrigator_Schematic.brd, AutoIrrigator_Schematic.sch, Rough_Draft_Schematic.brd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]
2020-11-26 added i2c address port scanner for finding i2c address on the bus
2020-11-26 moisure sensor test
2020-11-27 moisture sensor working and reading, water level sensor working and reading.
2020-11-27 fixed a couple compile bugs i didnt notice earlier
    [main.ino]
2020-11-27 currently working code, wls, pump, moisture sensor all programed.
2020-12-06 added a printout of esp IP address once connected to wifi
2020-12-06 added error printing functions and number conversion functions, need to clean up utility_sys with unneeded macros
    [main.c]
2020-12-07 user program sending messages to esp for changing moisture threshold and pump time. ESP stores the new value into the EEPROM and data struct
